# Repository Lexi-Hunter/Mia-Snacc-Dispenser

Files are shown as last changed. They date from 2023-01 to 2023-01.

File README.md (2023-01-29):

# Mia-Snacc-Dispenser
A device that lets you monitor your pet and dispense treats to them
 
<p align="center">
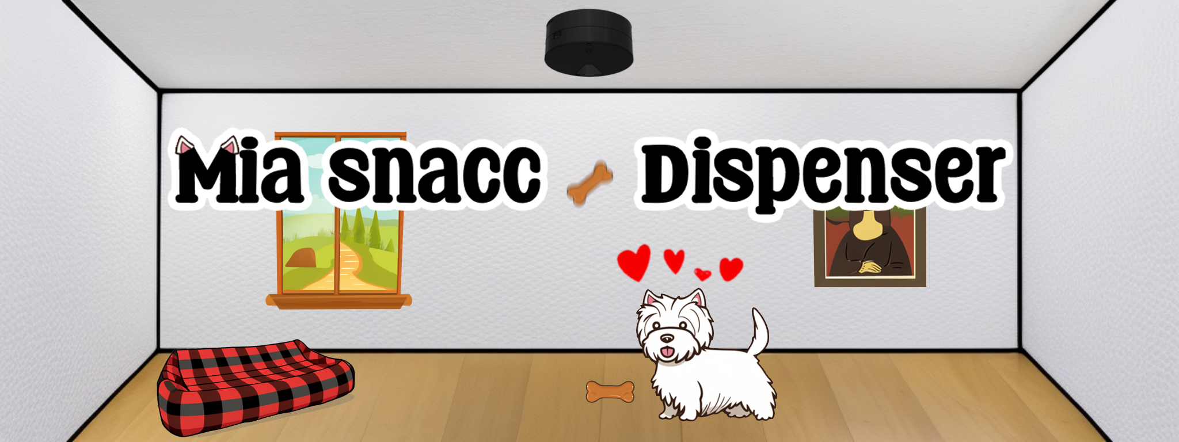
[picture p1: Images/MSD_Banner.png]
  
</p>

## What is the Mia Snacc Dispenser?
The Mia Snacc Dispenser (MSD) is a passion project that I worked on that allows a user to see a live feed of their pet, and then press a button to dispense a treat.
I was motivated to build this device as multiple family members in our house moved away at around the same time, whilst our dog Mia stayed behind. The MSD allows all of my family members to see and interact with Mia regardless of where they are in the world and therefore feel a greater sense of connection.

## How does it work?
A Raspberry Pi Zero W is used to create the site interface along with a Raspberry Pi camera module to capture the live stream. The device is attached to the ceiling so that its contents are out of reach, and so that upon being dispensed, the treat will then drop down and be accessible. A stepper motor is responsible for moving all the treats within the storage area and to dispense exactly one item.

## Site interface
<p align="center">
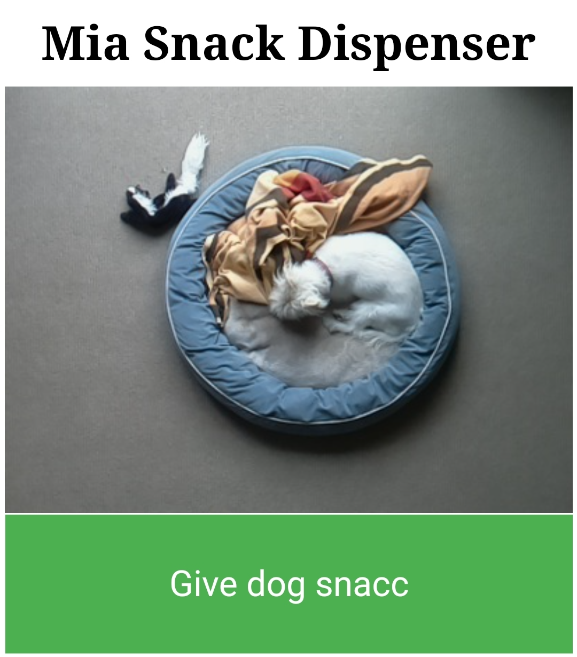
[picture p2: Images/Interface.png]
 
</p>

## Real World Implementation
Here is what the device looks like when it is installed on a ceiling:
<p align="center">
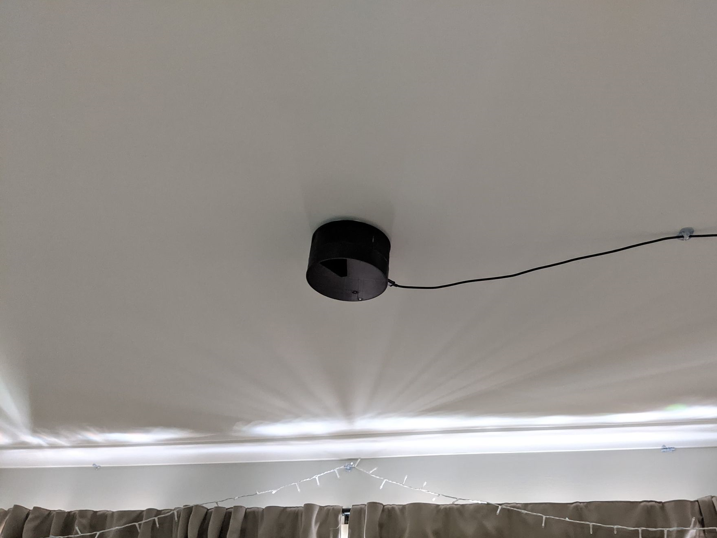
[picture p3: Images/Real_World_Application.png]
 
</p>

## Demo Video
Here is a screen recording of the device being used. Multiple users can access the page simultaneously and dispense treats. In the video my sister and I are both dispensing treats by pressing the button (which is why some treats are dispensed when the button isn't pressed in the recording)

MSD Video (https://www.youtube.com/watch?v=GJGxbpRRaEQ)

## How do treats get dispensed?
The device was originally intended to store and dispense sliced carrots as this would be a healthy but tasty option, but upon experimentation, carrots were found to produce too much friction within the mechanism, and the carrot slices would expire faster than anticipated. It was decided that solid dry dog treats would be ideal as they would solve both of these problems.

The V1 of the MSD could store 21 carrot slices by having three platters sitting on top of each other, with 8 rods which can move freely on each platter. This design works by having each rod pushing on a carrot slice around the platter until finally falling onto the platter on the next layer down.

Here is an animation for how this storage and retrieval system works:



The V2 of the MSD improved upon the first iteration by changing to a substance with a greater shelf life and less friction, whilst also having a smaller volume, allowing for a total of 30 treats stored at once.

Here is the improved design which stores spherical dog treats:
<p align="center">
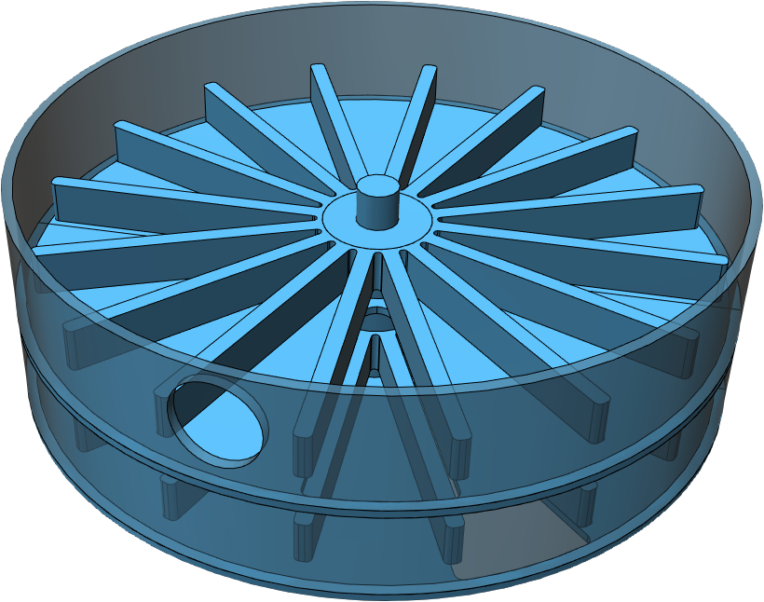
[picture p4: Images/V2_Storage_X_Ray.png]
 
</p>

## 3D Printing
In the 3D-Models folder there are the following 4 files that need to be printed and then assembled:
<p align="center">
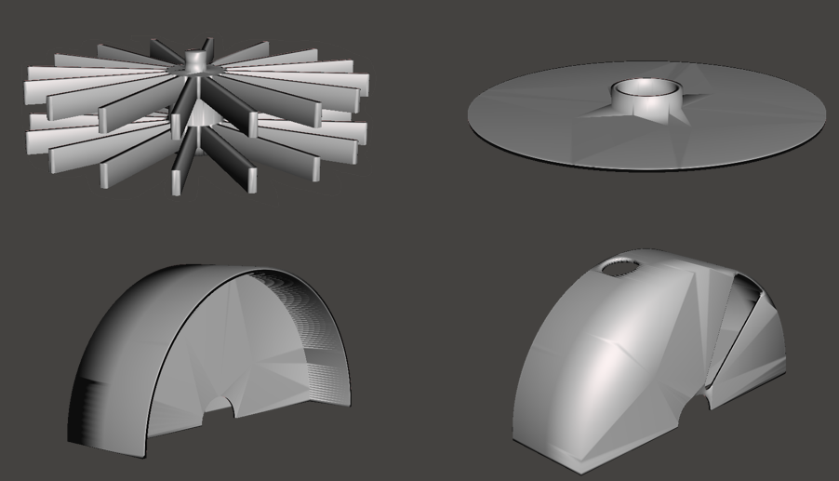
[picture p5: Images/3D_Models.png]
 
</p>

## Electronics
Here is an xray view of the underside of the device, where the electronics are stored:

<p align="center">
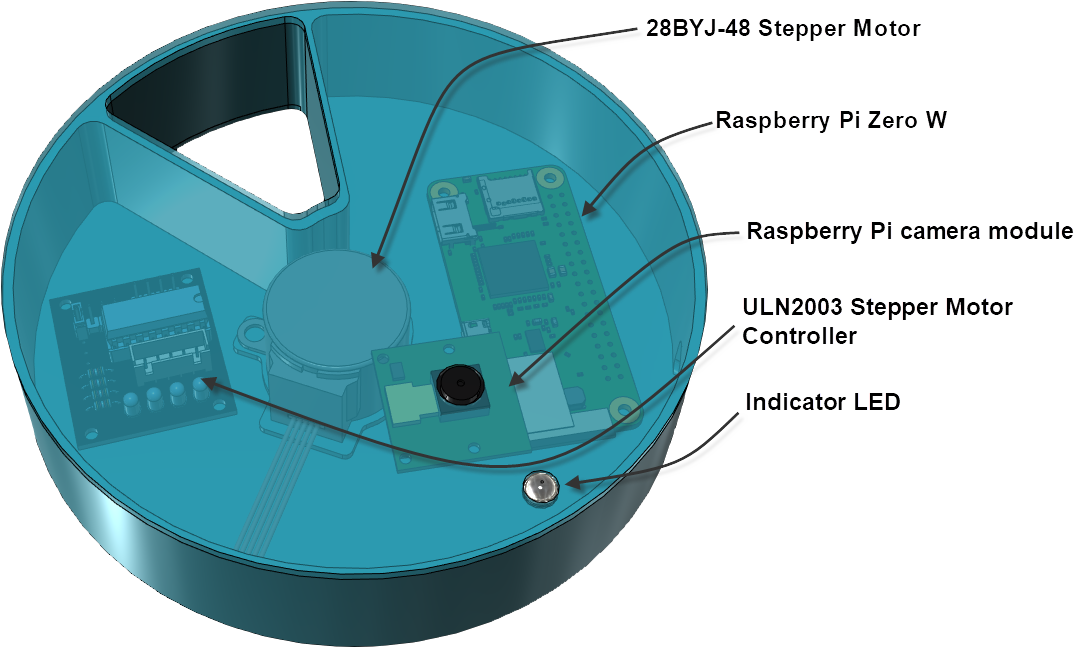
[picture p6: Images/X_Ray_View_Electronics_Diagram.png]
 
</p>

## Software
To replicate this project you'll need some basic knowledge of Raspberry Pi, setting up the OS, enabling the camera, etc. Once you have all the basics set up, simply run the Mia_Snacc_Dispenser.py file and it will come to life! It is most useful if you set the python file to auto launch upon booting up, so as soon as the device receives power, it'll auto start the program and just work!

<p align="center">
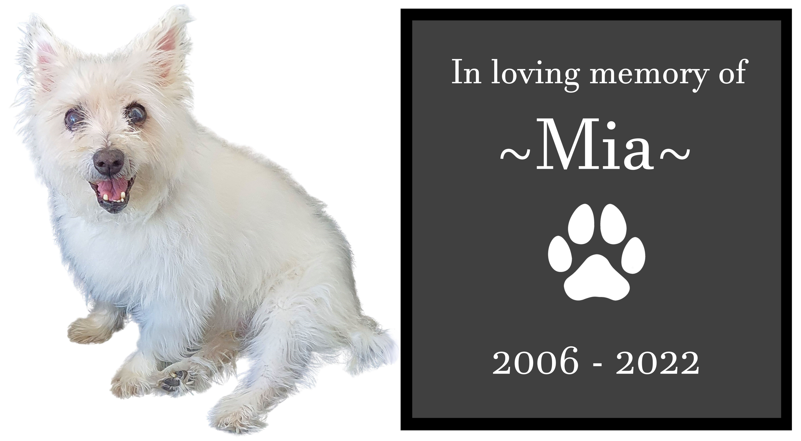
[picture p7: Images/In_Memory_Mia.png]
 
</p>

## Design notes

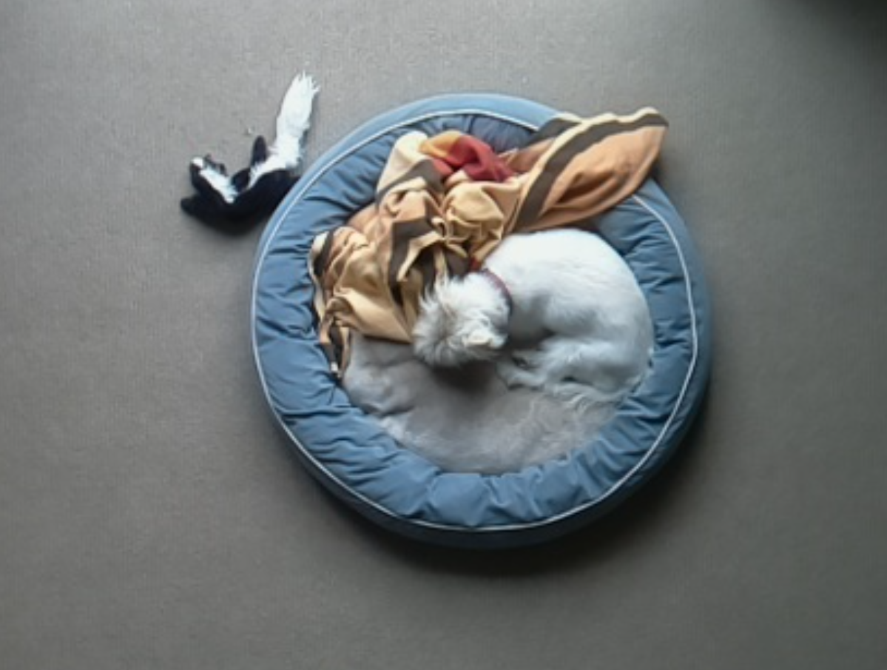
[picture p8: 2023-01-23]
Images/Aerial_View.png

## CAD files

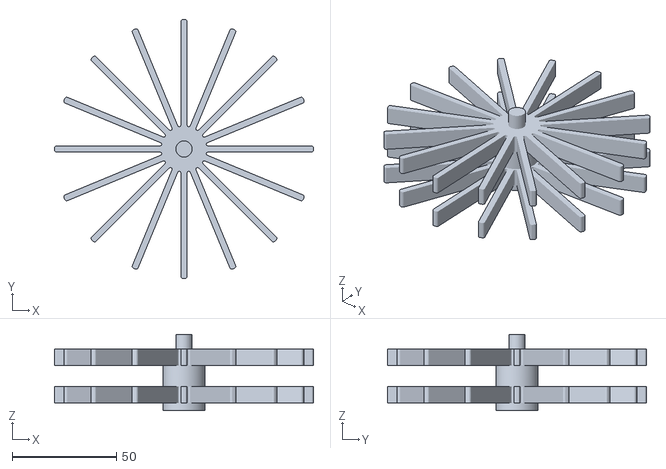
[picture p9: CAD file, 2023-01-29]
3D-Models/Combined_Pushers.stl
124.3 x 124.3 x 36.5

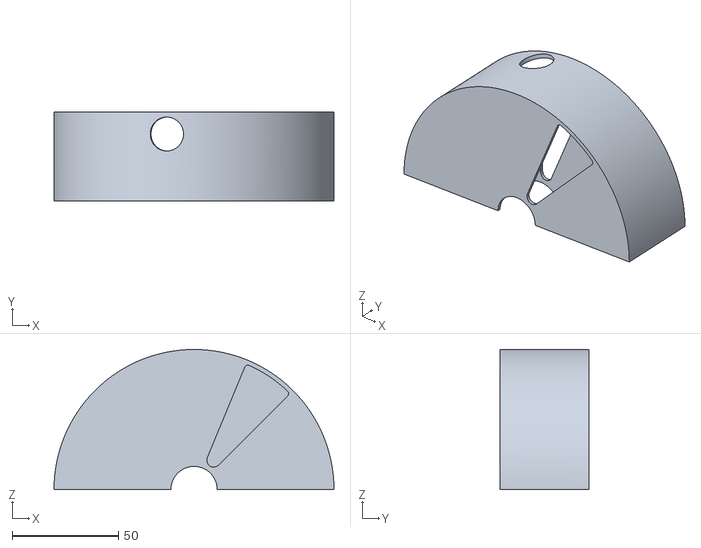
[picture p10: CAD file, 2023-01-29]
3D-Models/Right_Shell.stl
132.0 x 41.8 x 66.0

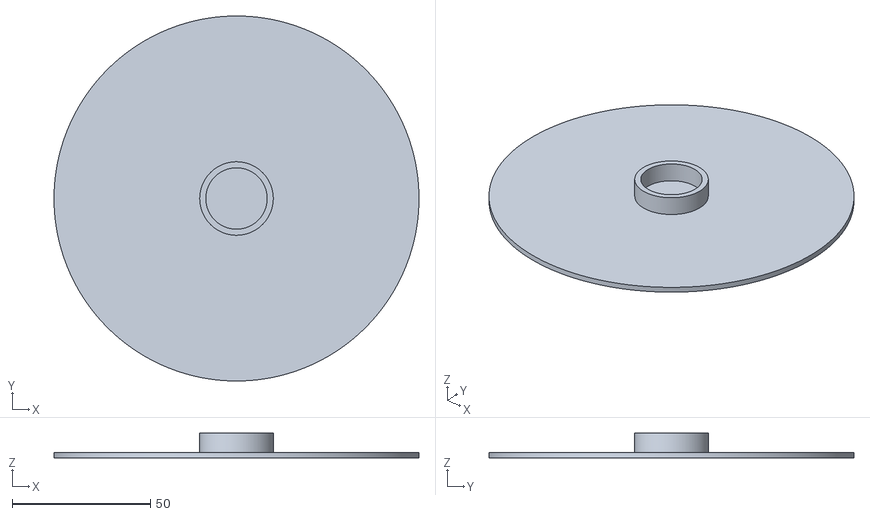
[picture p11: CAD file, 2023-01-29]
3D-Models/Top_Roof.stl
132.0 x 132.0 x 9.00

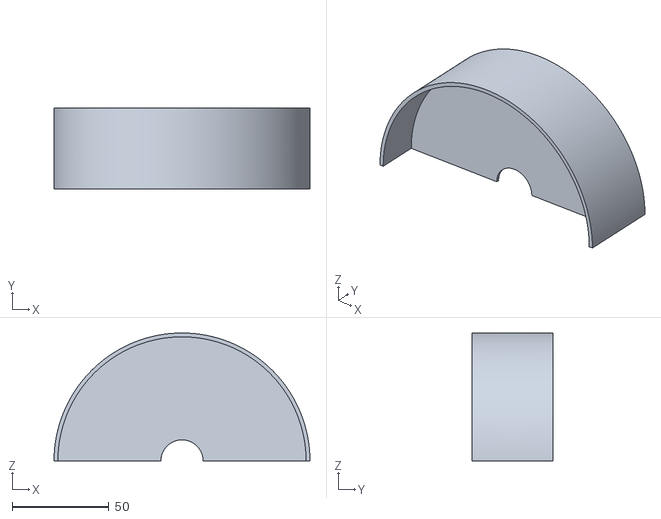
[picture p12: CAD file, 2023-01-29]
3D-Models/Left_Shell.stl
132.0 x 41.8 x 66.0

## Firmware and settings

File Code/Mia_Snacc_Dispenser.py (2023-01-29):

# Web streaming code modified from: http://picamera.readthedocs.io/en/latest/recipes2.html#web-streaming

import io
import picamera
import logging
import socketserver
import RPi.GPIO as GPIO
from threading import Condition
from http import server
import time

ControlPins = [7, 11, 13, 15]

GPIO.setmode(GPIO.BOARD)

GPIO.setup(37, GPIO.OUT)
GPIO.output(37, 0)

for pin in ControlPins:
	GPIO.setup(pin, GPIO.OUT)
	GPIO.output(pin, 0)

seq = [
    [1,1,0,0],
    [0,1,1,0],
    [0,0,1,1],
    [1,0,0,1]
]

def refill():
    for i in range(30):
        time.sleep(2)
        giveTreat(refill=True)

def giveTreat(refill=False):
    GPIO.output(37,1)
    time.sleep(0.5)
    GPIO.output(37,0)

    if not refill:
        #Flash light
        for i in range(3):
            GPIO.output(37,1)
            time.sleep(0.5)
            GPIO.output(37,0)
            time.sleep(0.5)
    #Spin backwards briefly
    for i in range(10):
        for seq_step in seq[::-1]:
            for index, val in enumerate(seq_step):
                GPIO.output(ControlPins[index], val)
                time.sleep(0.002)
    #Spin forwards
    for i in range(32+10):
        for seq_step in seq:
            for index, val in enumerate(seq_step):
                GPIO.output(ControlPins[index], val)
                time.sleep(0.002)
    for pin in ControlPins:
        GPIO.output(pin,0)
    
    if not refill:
        time.sleep(5)

PAGE="""\
<html>
<head>
<style>
.button {
  background-color: #4CAF50; /* Green */
  border: none;
  color: white;
  padding: 15px 64px;
  text-align: center;
  text-decoration: none;
  display: inline-block;
  font-size: 60px;
  margin: 4px 2px;
  cursor: pointer;
  width: 100%;
  height: 13%
}

h1 {
  font-size: 80;
}

img {
  width: 100%;
  height: auto;
}


</style>
<title>Mia Snack Dispenser</title>
</head>
<body>
<center><h1>Mia Snack Dispenser</h1></center>
<center><img src="stream.mjpg" width="320" height="240"></center>
<center><a href="/on" target="_parent"><button class="button">Give dog snacc</button></a></center>
</body>
</html>
"""

class StreamingOutput(object):
    def __init__(self):
        self.frame = None
        self.buffer = io.BytesIO()
        self.condition = Condition()

    def write(self, buf):
        if buf.startswith(b'\xff\xd8'):
            # New frame, copy the existing buffer's content and notify all
            # clients it's available
            self.buffer.truncate()
            with self.condition:
                self.frame = self.buffer.getvalue()
                self.condition.notify_all()
            self.buffer.seek(0)
        return self.buffer.write(buf)

class StreamingHandler(server.BaseHTTPRequestHandler):
    def do_GET(self):
        if self.path == '/':
            self.send_response(301)
            self.send_header('Location', '/index.html')
            self.end_headers()
            
        elif self.path == '/index.html':
            content = PAGE.encode('utf-8')
            self.send_response(200)
            self.send_header('Content-Type', 'text/html')
            self.send_header('Content-Length', len(content))
            self.end_headers()
            
            self.wfile.write(content)
        elif self.path == '/stream.mjpg':
            self.send_response(200)
            self.send_header('Age', 0)
            self.send_header('Cache-Control', 'no-cache, private')
            self.send_header('Pdaragma', 'no-cache')
            self.send_header('Content-Type', 'multipart/x-mixed-replace; boundary=FRAME')
            self.end_headers()

            try:
                while True:
                    with output.condition:
                        output.condition.wait()
                        frame = output.frame
                    self.wfile.write(b'--FRAME\r\n')
                    self.send_header('Content-Type', 'image/jpeg')
                    self.send_header('Content-Length', len(frame))
                    self.end_headers()
                    self.wfile.write(frame)
                    self.wfile.write(b'\r\n')
                    # Turn Green light on
                    #GPIO.output(37,1)

            except Exception as e:
                logging.warning(
                    'Removed streaming client %s: %s',
                    self.client_address, str(e))
                # Turn green light off
                #GPIO.output(37,0)
        elif self.path == '/on':
            giveTreat()
            content = PAGE.encode('utf-8')
            self.send_response(200)
            self.send_header('Content-Type', 'text/html')
            self.send_header('Content-Length', len(content))
            self.end_headers()
            self.wfile.write(content)

        elif self.path == '/refill':
            refill()
            content = PAGE.encode('utf-8')
            self.send_response(200)
            self.send_header('Content-Type', 'text/html')
            self.send_header('Content-Length', len(content))
            self.end_headers()
            self.wfile.write(content)

        else:
            self.send_error(404)
            self.end_headers()

class StreamingServer(socketserver.ThreadingMixIn, server.HTTPServer):
    allow_reuse_address = True
    daemon_threads = True

with picamera.PiCamera(resolution='320x240', framerate=24) as camera:
    output = StreamingOutput()
    #Uncomment the next line to change your Pi's Camera rotation (in degrees)
    #camera.rotation = 90
    camera.start_recording(output, format='mjpeg')
    try:
        address = ('', 8000)
        server = StreamingServer(address, StreamingHandler)
        server.serve_forever()
    finally:
        camera.stop_recording()
        GPIO.cleanup()
